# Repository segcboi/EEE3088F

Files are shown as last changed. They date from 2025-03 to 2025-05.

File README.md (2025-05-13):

# EEE3088F Group 9 Micro-Mouse Power Subsystem 

The object of this project is to design a power subsystem that will be able to power a multitude of functions of a maze-solving Micro-Mouse for our EEE3088F Engineering Design Principles course.  

## Requirements
- Operate four motors bidirectionally
- Monitor battery using the INA219
- Charge the battery using 9 V
- Have both 200 mA and 600 mA charging modes
- Provide 3V3 and 5V
- Integrate a USB-C port for charging
- Provide external load switching
- Provide a switch to turn off the system

## Layout
The layout of files for the project are as follows:
### Datasheets
This is where all component datasheets are located.
### Power_Board_v2
This is whare the PCB schematics and design are located
### Library.pretty
This is where certain components's footprints can be located, mainly the switch and __________ since KiCad had no stored footprint for the required switch and_________.

## External Sources
Certain external sources were used to make life and the design process slightly easier. These included
- Bouni's Repo: This gave access to a multitude of features that allowed KiCad access to a whole host of components from JLCPCB's parts library.
- The devil: We sold our souls to the devil himself to actually get this design completed.

## Design Tools
The design of the PCB was done using the free PCB desgin software KiCad.

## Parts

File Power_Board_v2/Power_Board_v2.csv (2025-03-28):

Reference | Qty | Value | DNP | Exclude from BOM | Exclude from Board | Footprint | Datasheet
C4,C8 | 2 | 4.7u |  |  |  | Capacitor_SMD:C_0603_1608Metric_Pad1.08x0.95mm_HandSolder | ~
C5,C6,C7 | 3 | 1u |  |  |  | Capacitor_SMD:C_0603_1608Metric_Pad1.08x0.95mm_HandSolder | ~
D1 | 1 | LEDW |  |  |  | LED_SMD:LED_0603_1608Metric_Pad1.05x0.95mm_HandSolder | ~
D2 | 1 | LEDR |  |  |  | LED_SMD:LED_0603_1608Metric_Pad1.05x0.95mm_HandSolder | ~
J1 | 1 | PH2.54-01-16PZS |  |  |  | Connector_PinHeader_2.54mm:PinHeader_2x16_P2.54mm_Vertical | ~
Q1 | 1 | MMBT5551L |  |  |  | Package_TO_SOT_SMD:SOT-23 | www.onsemi.com/pub/Collateral/MMBT5550LT1-D.PDF
R2 | 1 | 75k |  |  |  | Resistor_SMD:R_0603_1608Metric_Pad0.98x0.95mm_HandSolder | ~
R3 | 1 | 4k3 |  |  |  | Resistor_SMD:R_0603_1608Metric_Pad0.98x0.95mm_HandSolder | ~
R4 | 1 | 150R |  |  |  | Resistor_SMD:R_0805_2012Metric_Pad1.20x1.40mm_HandSolder | ~
R7,R10,R16 | 3 | 10k |  |  |  | Resistor_SMD:R_0603_1608Metric_Pad0.98x0.95mm_HandSolder | ~
R9,R11,R12,R13,R15,R18 | 6 | 1k5 |  |  |  | Resistor_SMD:R_0603_1608Metric_Pad0.98x0.95mm_HandSolder | ~
R14,R17 | 2 | 0.4R |  |  |  | Resistor_SMD:R_1206_3216Metric_Pad1.30x1.75mm_HandSolder | ~
TP1,TP2,TP3,TP4,TP5,TP6 | 6 | TestPoint |  |  |  | TestPoint:TestPoint_Pad_D3.0mm | ~
U2 | 1 | HUSB237-AA001-DN06R |  |  |  | Package_DFN_QFN:DFN-6-1EP_2x2mm_P0.65mm_EP1.01x1.7mm | kicad-embed://HUSB237.pdf
U3 | 1 | BQ24074RGT |  |  |  | Package_DFN_QFN:VQFN-16-1EP_3x3mm_P0.5mm_EP1.6x1.6mm | http://www.ti.com/lit/ds/symlink/bq24074.pdf
U4 | 1 | INA219AIDCNR |  |  |  | Package_TO_SOT_SMD:SOT-23-8 | http://www.ti.com/lit/ds/symlink/ina219.pdf
USBC1 | 1 | TYPE-C-31-M-12 |  |  |  | Connector_USB:USB_C_Receptacle_HRO_TYPE-C-31-M-12 | https://atta.szlcsc.com/upload/public/pdf/source/20220525/466408E853115E789EDB0DDC29077C05.pdf

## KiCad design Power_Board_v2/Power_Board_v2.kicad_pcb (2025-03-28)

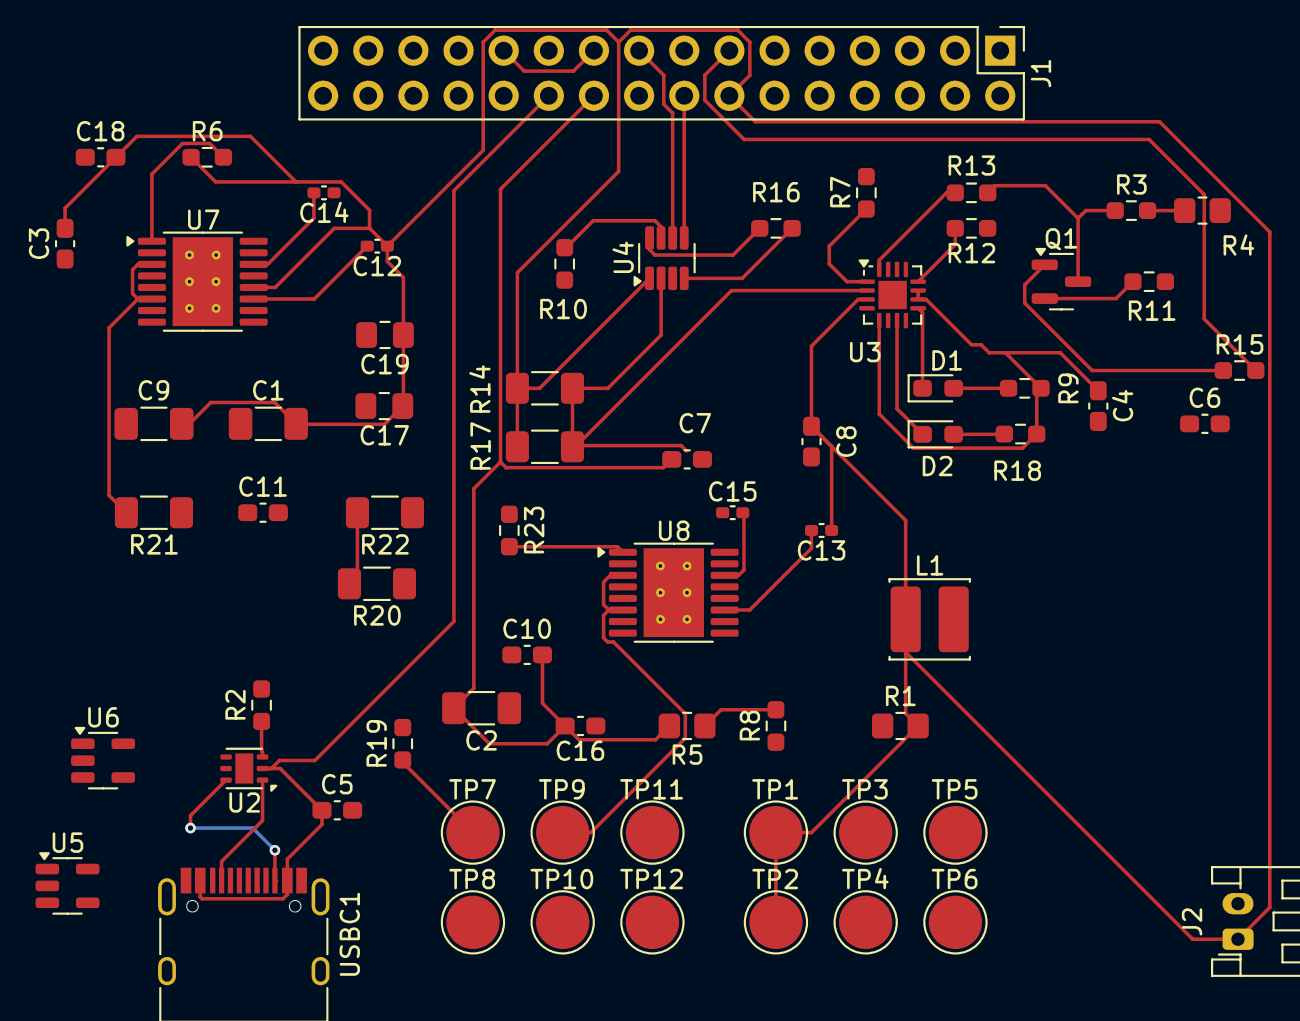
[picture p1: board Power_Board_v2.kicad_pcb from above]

Board: 2 copper layers, 68 parts (0 on the bottom side), 52 nets.

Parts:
C1, C2: 22uF; C_1206_3216Metric_Pad1.33x1.80mm_HandSolder
C3, C11: 4.7uF; C_0603_1608Metric_Pad1.08x0.95mm_HandSolder
C4, C8: 4.7u; C_0603_1608Metric_Pad1.08x0.95mm_HandSolder
C5, C6, C7: 1u; C_0603_1608Metric_Pad1.08x0.95mm_HandSolder
C9: 100uF; C_1206_3216Metric_Pad1.33x1.80mm_HandSolder
C10, C16, C18: 1uF; C_0603_1608Metric_Pad1.08x0.95mm_HandSolder
C12, C13: 10nF; C_0402_1005Metric_Pad0.74x0.62mm_HandSolder
C14, C15: 2.2uF; C_0402_1005Metric_Pad0.74x0.62mm_HandSolder
C17, C19: 10uF; C_0805_2012Metric_Pad1.18x1.45mm_HandSolder
D1: LEDW; LED_0603_1608Metric_Pad1.05x0.95mm_HandSolder
D2: LEDR; LED_0603_1608Metric_Pad1.05x0.95mm_HandSolder
J1: PH2.54-01-16PZS; PinHeader_2x16_P2.54mm_Vertical
J2: Conn_01x02; JST_PH_S2B-PH-K_1x02_P2.00mm_Horizontal
L1: SWPA4020S1R5NT; L_Cenker_CKCS4018
Q1: MMBT5551L; SOT-23
R1, R5: 1MΩ; R_0805_2012Metric_Pad1.20x1.40mm_HandSolder
R2: 75k; R_0603_1608Metric_Pad0.98x0.95mm_HandSolder
R3: 4k3; R_0603_1608Metric_Pad0.98x0.95mm_HandSolder
R4: 150R; R_0805_2012Metric_Pad1.20x1.40mm_HandSolder
R6, R19, R23: 10kΩ; R_0603_1608Metric_Pad0.98x0.95mm_HandSolder
R7, R10, R16: 10k; R_0603_1608Metric_Pad0.98x0.95mm_HandSolder
R8: 330kΩ; R_0603_1608Metric_Pad0.98x0.95mm_HandSolder
R9, R11, R12, R13, R15, R18: 1k5; R_0603_1608Metric_Pad0.98x0.95mm_HandSolder
R14, R17: 0.4R; R_1206_3216Metric_Pad1.30x1.75mm_HandSolder
R20, R21, R22: 1Ω; R_1206_3216Metric_Pad1.30x1.75mm_HandSolder
TP1, TP2, TP3, TP4, TP5, TP6, TP7, TP8, TP9, TP10, TP11, TP12: TestPoint; TestPoint_Pad_D3.0mm
U2: HUSB237-AA001-DN06R; DFN-6-1EP_2x2mm_P0.65mm_EP1.01x1.7mm
U3: BQ24074RGT; VQFN-16-1EP_3x3mm_P0.5mm_EP1.6x1.6mm
U4: INA219AIDCNR; SOT-23-8
U5, U6: RT9742GGJ5; TSOT-23-5
U7, U8: DRV8833PWP; HTSSOP-16-1EP_4.4x5mm_P0.65mm_EP3.4x5mm_Mask2.46x2.31mm_The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
USBC1: TYPE-C-31-M-12; USB_C_Receptacle_HRO_TYPE-C-31-M-12

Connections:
/3V3 Out: C11.2, J1.18
/5V Out: C2.2, C7.1, C10.2, C16.2, J1.20, R5.2, R16.1, U4.4 (VS)
/Battery: C1.2, C3.2, C8.2, C9.2, C12.1, C13.1, C17.1, C18.2, C19.1, J1.14, J2.1, L1.1, R1.2, R6.1, R14.1, R14.2, R17.1, R17.2, R23.1, TP1.1, TP2.1, U3.2 (BAT), U3.3 (BAT), U4.1 (IN+), U4.2 (IN-), U7.12 (VM), U8.12 (VM)
/FAST_CHARGE_CTRL: J1.13, R15.2
/High Voltage (9V): C5.1, C6.1, J1.22, U2.2 (VUSB), U3.13 (IN), USBC1.A4 (VBUS), USBC1.A9 (VBUS), USBC1.B4 (VBUS), USBC1.B9 (VBUS)
/I2C1_SCL: J1.16, U4.5 (SCL)
/I2C1_SDA: J1.17, U4.6 (SDA)
/LOAD: C4.1, R9.1, R18.1, U3.5 (EN2), U3.10 (OUT), U3.11 (OUT)
/MOTOR1_A_OUT: J1.32, U7.2 (AOUT1)
/MOTOR1_B_OUT: J1.31, U7.4 (AOUT2)
/MOTOR1_CTRL1: J1.28, U7.16 (AIN1)
/MOTOR1_CTRL2: J1.30, U7.15 (AIN2)
/MOTOR2_CTRL1: J1.4, U7.9 (BIN1)
/MOTOR2_CTRL2: J1.6, U7.10 (BIN2)
/MOTOR3_A_OUT: J1.27, U8.2 (AOUT1)
/MOTOR3_B_OUT: J1.29, U8.4 (AOUT2)
/MOTOR3_CTRL1: J1.24, U8.16 (AIN1)
/MOTOR3_CTRL2: J1.26, U8.15 (AIN2)
/MOTOR4_CTRL1: J1.8, U8.9 (BIN1)
/MOTOR4_CTRL2: J1.10, U8.10 (BIN2)
/Motor2_A_OUT: J1.2, U7.7 (BOUT1)
/Motor2_B_OUT: J1.1, U7.5 (BOUT2)
/Motor4_A_OUT: J1.3, U8.7 (BOUT1)
/Motor4_B_OUT: J1.5, U8.5 (BOUT2)
GND: C1.1, C2.1, C3.1, C4.2, C5.2, C7.2, C8.1, C9.1, C10.1, C11.1, C14.1, C15.1, C16.1, C17.2, C18.1, C19.2, J1.19, J1.23, J2.2, R1.1, R2.2, R4.2, R7.2, R8.1, R10.2, R11.2, R12.1, R19.2, R20.1, R21.1, R22.1, TP4.1, TP8.1, TP10.1, TP12.1, U2.7 (GND), U3.8 (VSS), U3.17 (VSS), U4.3 (GND), U7.13 (GND), U7.17 (GND), U8.13 (GND), U8.17 (GND), USBC1.A1 (GND), USBC1.A12 (GND), USBC1.B1 (GND), USBC1.B12 (GND)
unnamed: D1.2 (A), R9.2
unnamed: D1.1 (K), U3.9 (~CHG)
unnamed: D2.2 (A), R18.2
unnamed: D2.1 (K), U3.7 (~PGOOD)
unnamed: Q1.1 (B), R15.1
unnamed: Q1.3 (C), R3.1, R13.1, TP3.1
unnamed: Q1.2 (E), R11.1, TP5.1
unnamed: R3.2, R4.1
unnamed: R19.1, TP7.1
unnamed: R5.1, R8.2
unnamed: U2.1 (CC1), USBC1.A5 (CC1)
unnamed: U2.6 (CC2), USBC1.B5 (CC2)
unnamed: R2.1, U2.3 (VSET)
unnamed: C6.2, TP6.1, U3.4 (~CE), U3.6 (EN1), U3.14 (TMR)
unnamed: R12.2, U3.12 (ILIM)
unnamed: R13.2, U3.16 (ISET)
unnamed: R7.1, U3.1 (TS)
unnamed: R10.1, U4.7 (A0)
unnamed: R16.2, U4.8 (A1)
unnamed: R21.2, TP11.1, U7.3 (AISEN), U7.6 (BISEN)
unnamed: C12.2, U7.11 (VCP)
unnamed: C14.2, U7.14 (VINT)
unnamed: R6.2, U7.1 (~SLEEP)
unnamed: R20.2, R22.2, TP9.1, U8.3 (AISEN), U8.6 (BISEN)
unnamed: C13.2, U8.11 (VCP)
unnamed: C15.2, U8.14 (VINT)
unnamed: R23.2, U8.1 (~SLEEP)

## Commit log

2025-03-27 Added my schematic files via upload
    [Power_Board_SMTJOS022xBHYEBR002.kicad_pcb, Power_Board_SMTJOS022xBHYEBR002.kicad_sch]
2025-03-27 Full project upload with biased ICs and feet
    [Power_Board_SMTJOS022xBHYEBR002.csv, Power_Board_SMTJOS022xBHYEBR002.kicad_pcb, Power_Board_SMTJOS022xBHYEBR002.kicad_sch]
2025-03-27 Power Board v2 upload
    This upload is just an updated Power Board schematic because the PCB editor was tweaking and not displaying the footprints
    [Power_Board_v2.kicad_pcb, Power_Board_v2.kicad_sch]
2025-03-27 Moved Stuff
    [Power_Board_v2.kicad_pcb, Power_Board_v2.kicad_sch]
2025-03-27 Removed some duplicates
    [Power_Board_SMTJOS022xBHYEBR002.csv, Power_Board_SMTJOS022xBHYEBR002.kicad_pcb, Power_Board_SMTJOS022xBHYEBR002.kicad_sch]
2025-03-27 Delete Project directory
    This was nonsense and needed to be removed
    [Power_Board_SMTJOS022xBHYEBR002.csv, Power_Board_SMTJOS022xBHYEBR002.kicad_pcb, Power_Board_SMTJOS022xBHYEBR002.kicad_sch]
2025-03-27 Delete Power_Board_SMTJOS022xBHYEBR002 directory
    Yes
    [Power_Board_SMTJOS022xBHYEBR002.kicad_pcb, Power_Board_SMTJOS022xBHYEBR002.kicad_sch]
2025-03-28 Did some PCB work
    [Power_Board_v2.kicad_pcb, Power_Board_v2.kicad_sch]
2025-03-28 More PCB work
    [Power_Board_v2.kicad_pcb]
2025-03-28 Space Saving
    Moved my things around to make space for Ebi's work
    [Power_Board_v2.kicad_pcb]
2025-03-28 Fixed up some errors
    [Power_Board_v2.kicad_pcb]
2025-03-28 Updated footprints and battery label
    I HATE THE IMPERIAL SYSTEM
    [Power_Board_v2.kicad_pcb, Power_Board_v2.kicad_sch]
2025-03-28 Updated parts' details to get correct BOM
    [Power_Board_v2.csv, Power_Board_v2.kicad_sch]
2025-03-28 Same as previous
    [Power_Board_v2.kicad_pcb, Power_Board_v2.kicad_sch]
2025-03-28 Updated some stuffs
    Tried to add the battery connector, but it wouldn't work
    [Power_Board_v2.kicad_pcb, Power_Board_v2.kicad_sch]
2025-03-28 Minor tweaks
    [Power_Board_v2.kicad_pcb, Power_Board_v2.kicad_sch]
2025-03-28 STARTED EBI WIRING
    [Power_Board_v2.kicad_pcb]
2025-03-28 STARTED EBI WIRING 2
    [Power_Board_v2.kicad_pcb]
2025-03-28 yes 3
    [Power_Board_v2.kicad_sch]
2025-03-28 Connected up the last passive stuff
    [Power_Board_v2.kicad_pcb]
